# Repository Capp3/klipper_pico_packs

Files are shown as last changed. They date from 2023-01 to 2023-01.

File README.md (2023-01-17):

# klipper_pico_packs

## Pico Packs for use with Klipper 3D printing firmware

This is a project to develop a secondary MCU for [Klipper3D](https://www.klipper3d.org/) using a [Raspberry Pi Pico](https://www.raspberrypi.com/products/raspberry-pi-pico/).

The genesis of this project is moving into Klipper with an older control board that wasnt built with all of the fancy interfacing that is avilable on purpose built Klipper boards. Or really just newer boards in general. My smoothie cone works well and I dont want to replace it just to add 

There are two flavours of packs here, a very tiny one meant to sit over top of a Pico with the same footprint. This has limited connectivity, but is quick and cheap, using connectors and bits I have laying about.

The "non-pico" is a larger pack meant to have the Pico sit on top of using the headers and can be bought pre-installed. This includes a larger assorment of connections and support components, notably some power regulation for driving Neopixels.

## Klipper problems with the RP2040

The RP2040 chip has had some documented problems related to reset with Klipper, I have implemented this solution;

### Workaround to connect rp2040 on startup or reboot

This is a *Work In Progess!!*

Install `uhubctl` a [utility for controlling USB power on the host microprocessor](https://github.com/mvp/uhubctl)

This may need to be adjusted for the specific USB port that the unit is connected to.

```bash
sudo apt install uhubctl
```

Next, edit `rc.local`

```bash
sudo nano /etc/rc.local
```

place this before `exit 0`

```bash
uhubctl -l 1-1 -a 2
sleep 1 && uhubctl -l 1-1 -a 2
```

## Pico Pack

Simple, simple, simple. This is mostly an exercise in develpment. This setup is mostly reflecting what I have put on a breadboard.

### Connections

SPI connections are seperated into "Data" and "Power" connectors. Both for space constrants. and because the assortment of JST connectors I have only go to 5 position!! Power connections include 2 GND positions to allow for grounding the shield of SPI, if present.

| Connector | Description | Klipper Pins | Pico Pins |
| --- | --- | --- | --- |
| J1 | VBUS(5v)/3.3v Power | NA | NA |
| J2 | VBUS(5v)/3.3v Power | NA | NA |
| J3 | SPI0 | spi0b | SPI0/1 |
| J4 | SPI1 | spi1a | SPI1/4 |
| J5 | IO0 | gpio27 | 32 |
| J6 | IO1 | gpio26 | 31 |
| J7 | I2C | i2c0f | 20/21 |

The board design includes provisions for adding i2c pullup resistors to 3.3v. i2c interface only compatible at 3.3v for supply and signal.

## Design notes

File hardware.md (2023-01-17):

# RPi Pico Hardware Reference information

## RPi Pico Hardware info

Information related to the Picos hardware and pin configs and how Klipper references them.

### Pico Pins

Find all Pico Pins here

[Pico Pinout Diagram](https://pico.pinout.xyz/)

### SPI Bus info

Two buses, but avilable on differnt pins. alias are as diffined in Klipper.

| Bus | Alias | RX/MISO | TX/MOSI | SCK | CS |
| --- | ----- | --- | --- | --- | --- |
| SPI0/0  | spi0a | gpio0 | gpio3 | gpio2  | gpio1  |
| SPI0/1  | spi0b | gpio4 | gpio7 | gpio6  | gpio5  |
| SPI0/2  | spi0c | gpio16  | gpio19  | gpio18 | gpio17 |
| SPI0/3* | spi0d | gpio20  | gpio23  | gpio22 | |
| ------- | ----- | ------- | ------- | ------ | ------ |
| SPI1/4  | spi1a | gpio8 | gpio11  | gpio10 | gpio9  |
| SPI1/5  | spi1b | gpio12  | gpio15  | gpio14 | gpio13 |
| SPI1/6* | spi1c | gpio24  | gpio27  | gpio26 | |

*- Pins are defined in the Klipper Code, but not marked on most Pico pinouts

### i2c Bus info

| Alias | SDA | SCL |
| ----- | -----  | --- |
| i2c0a | gpio0  | gpio1  |
| i2c0b | gpio4  | gpio5  |
| i2c0c | gpio8  | gpio9  |
| i2c0d | gpio12 | gpio13 |
| i2c0e | gpio16 | gpio17 |
| i2c0f | gpio20 | gpio21 |
| i2c0g | gpio24 | gpio25 |
| i2c0h | gpio28 | gpio29 |
| i2c1a | gpio2  | gpio3  |
| i2c1b | gpio6  | gpio7  |
| i2c1c | gpio10 | gpio11 |
| i2c1d | gpio14 | gpio15 |
| i2c1e | gpio18 | gpio19 |
| i2c1f | gpio22 | gpio23 |
| i2c1g | gpio26 | gpio27 |

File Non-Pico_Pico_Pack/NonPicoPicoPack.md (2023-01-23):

# Non-Pico Pico Pack

The bigger version. My intention is to do this both as SMD and THC as an exercise. And THC would be a lot easier to do at home without special equipment.

## Connections and Pins

### Power Input

12-24v DC input, produces ~3amp for use with a MIC29500 fixed voltage reg.

| Pin | Desc |
| --- | --- |
| 1 | 12-24 vdc Input |
| 2 | Ground |

An extra connection is included for powering the Pi using the Onboard 5V labeled "PI_PWR"

| Pin | Desc  |
| --- | ----- |
| 1 | 5 vdc |
| 2 | Gnd |

### BL Touch Connection

BL touch connection on a 5 pin JST

| Pin | Pico Pin | Description |
| --- | --- | --- |
| 1 | gpio22 | Probe |
| 2 | NA | GND |
| 3 | gpio28 | Servo |
| 4 | NA | 5V |
| 5 | NA | GND |

### FAN Connections

Fan connection controlled by gpios. Voltage is sames as supply (12-24v)

#### FAN0

| Pin | Pico Pin | Desc |
| --- | --- | ---- |
| 1 | NA | VDC  |
| 2 | gpio18 | GND  |

#### FAN1

| Pin | Pico Pin | Desc |
| --- | --- | ---- |
| 1 | NA | VDC  |
| 2 | gpio19 | GND  |

### IO Ports

Two general IO ports with no supporting circuitry, be careful! Can be used as ins or outs, intention for replay control

#### IO0

| Pin | Pico Pin |
| --- | --- |
| 1 | gpio26 |
| 2 | GND |

#### IO1

| Pin | Pico Pin |
| --- | --- |
| 1 | gpio27 |
| 2 | GND |

### SPI Connections

A little odd here. Seperated the data and power to accomidate the assotment of connectors I have. Added an extra GND to the power connection to allow for sinking the shield per the klipper docs on cabling. Have 2 ports here

#### SPI Power Jumper

Set the voltage for the SPI power connections. Make sure you understand this and the unit you are connecting!!

| Pin | Desc |
| --- | ---- |
| 1 | 5vdc |
| 2 | Common Power |
| 3 | Pi 3.3vdc |

#### SPI Power Connections

| Pin | Desc |
| --- | ---- |
| 1 | GND  |
| 2 | PWR  |
| 3 | GND  |

#### SPI0

| Pin | Pico Pin | Desc |
| --- | --- | ---- |
| 1 | gpio04 | MISO |
| 2 | gpio07 | MOSI |
| 3 | gpio06 | SCLK |
| 4 | gpio05 | CS |

#### SPI1

| Pin | Pico Pin | Desc |
| --- | --- | ---- |
| 1 | gpio08 | MISO |
| 2 | gpio11 | MOSI |
| 3 | gpio10 | SCLK |
| 4 | gpio09 | CS |

### I2C

2 12c connections with selectable power

#### i2c Power Jumper

| Pin | Desc |
| --- | ---- |
| 1 | 5vdc |
| 2 | Common Power |
| 3 | Pi 3.3vdc |

#### i2c Connectors

Connections

| Pin | Pico Pin | Desc |
| --- | --- | ---- |
| 1 | NA | Pwr  |
| 2 | gpio21 | SDA  |
| 3 | gpio20 | SCL  |
| 4 | NA | GND  |

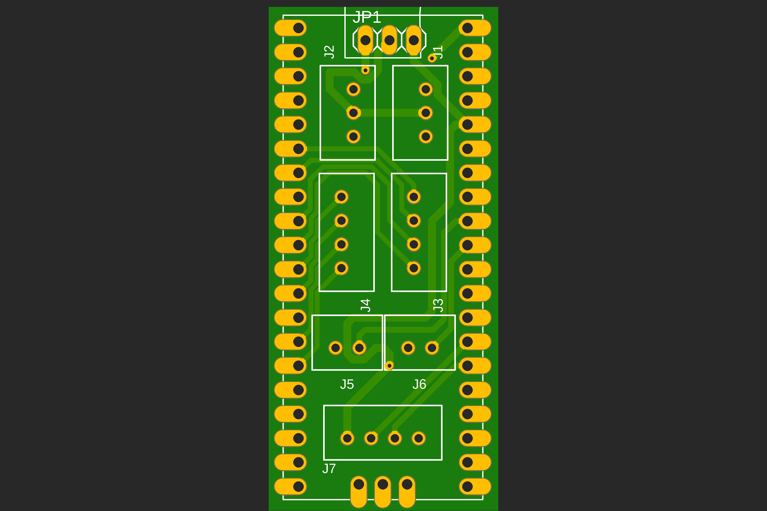
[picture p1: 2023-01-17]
Pico_Pack/PicoKlipperPack v6 Top.png

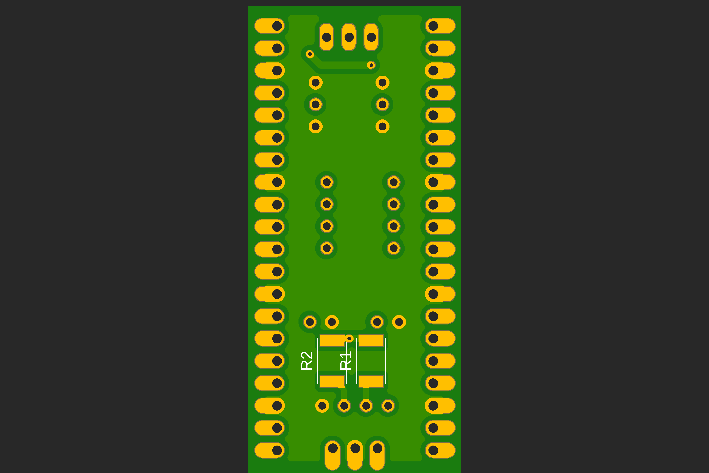
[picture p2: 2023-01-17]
Pico_Pack/PicoKlipperPack v6 Btm.png

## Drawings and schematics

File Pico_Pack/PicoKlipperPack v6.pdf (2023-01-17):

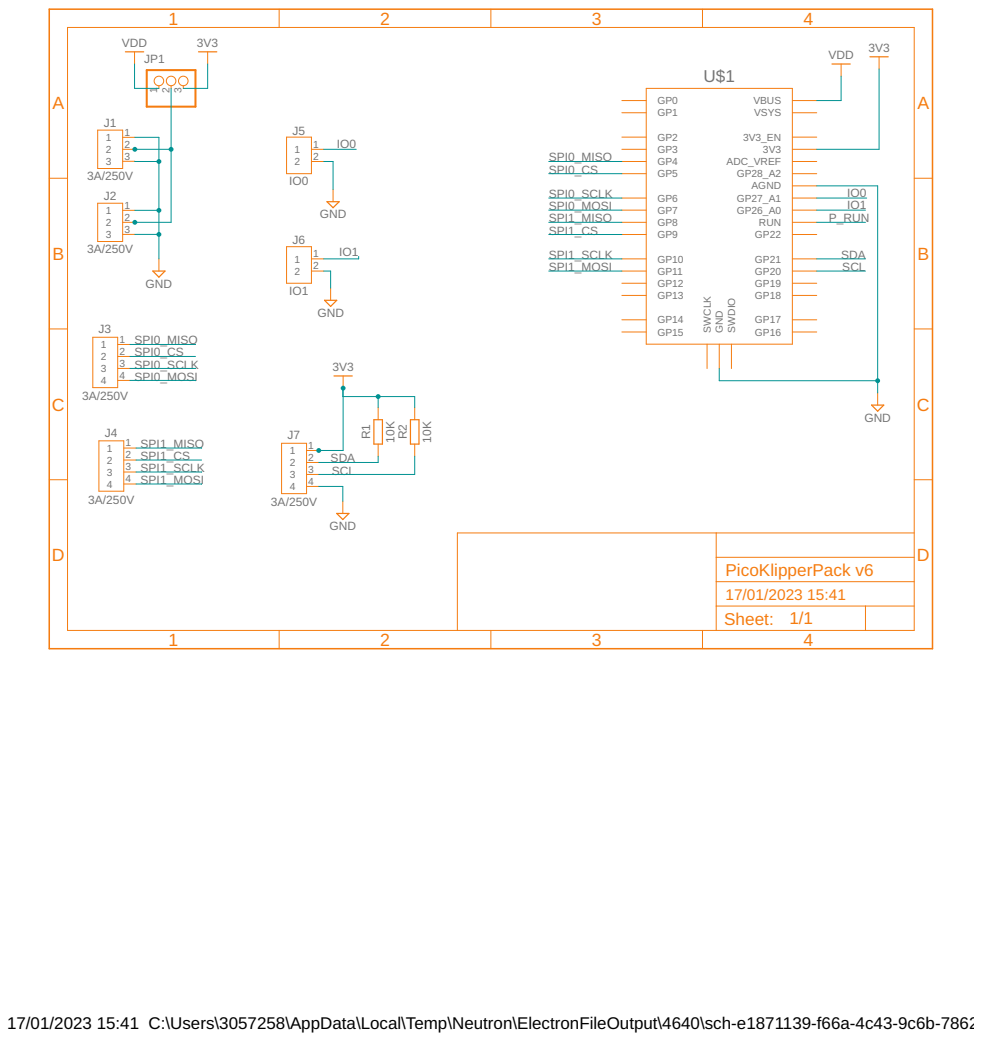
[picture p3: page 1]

17/01/2023 15:41 C:\Users\3057258\AppData\Local\Temp\Neutron\ElectronFileOutput\4640\sch-e1871139-f66a-4c43-9c6b-78624d30e3fe\PicoKlipperPack v6.sch (Sheet: 1/1)

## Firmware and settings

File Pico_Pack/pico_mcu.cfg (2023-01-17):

# Dont forget to add [include pico_mcu.cfg] to printer.cfg

# Define the new MCU. Refer to Klipper docs to locate the serial ID
[mcu aux]
serial: /dev/serial/by-id/usb-Klipper_rp2040_E66038B713776933-if00
restart_method: command

# Tese are the two avilable IO Pins, currently set as output pins. Use as needed
[output_pin aux_io0]
pin: aux:gpio27
value: 1
pwm: False

[output_pin aux_io1]
pin: aux:gpio26

[output_pin aux_beat]
### This is to provide a heartbeat on the LED that is onboard the pico
pin: aux:gpio25
value: .050
pwm: True

# Config for an i2c temp sensor, change if using different i2c device. 
[temperature_sensor room_temp]
sensor_type: BME280
i2c_address: 118
#   Default is 118 (0x76). Some BME280 sensors have an address of 119
#   (0x77).
#   The i2c address of the device. This must specified as a decimal
#   number (not in hex). The default depends on the type of device.
i2c_mcu: aux
#   The name of the micro-controller that the chip is connected to.
#   The default is "mcu".
i2c_bus: i2c0f
#   If the micro-controller supports multiple I2C busses then one may
#   specify the micro-controller bus name here. The default depends on
#   the type of micro-controller.
#i2c_speed:
#   The I2C speed (in Hz) to use when communicating with the device.
#   The Klipper implementation on most micro-controllers is hard-coded
#   to 100000 and changing this value has no effect. The default is
#   100000.

# [adxl345 hotend]
# cs_pin: aux:gpio5
# #   The SPI enable pin for the sensor. This parameter must be provided.
# #spi_speed: 5000000
# #   The SPI speed (in hz) to use when communicating with the chip.
# #   The default is 5000000.
# spi_bus: aux:spi0b
# #   Have read that when defining the spi_bus that the prefix of "aux:" may not work/matter. Need to evaluate.
# #axes_map: x, y, z
# #   The accelerometer axis for each of the printer's X, Y, and Z axes.
# #   This may be useful if the accelerometer is mounted in an
# #   orientation that does not match the printer orientation. For
# #   example, one could set this to "y, x, z" to swap the X and Y axes.
# #   It is also possible to negate an axis if the accelerometer
# #   direction is reversed (eg, "x, z, -y"). The default is "x, y, z".

# [adxl345 bed]
# cs_pin: aux:gpio9
# #spi_speed: 5000000
# spi_bus: aux:spi1a
# #axes_map: x, y, z

# [resonance_tester]
# accel_chip_x: adxl345 hotend
# accel_chip_y: adxl345 bed
# probe_points: 100, 100, 40
